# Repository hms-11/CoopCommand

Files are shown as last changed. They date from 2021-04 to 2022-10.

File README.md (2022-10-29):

# CoopCommand

# Development on this project has stopped. See [CoopCommand ESP32](https://github.com/hms-11/CoopCommandESP32) for the next generation controller and code.

Chickens are simple animals with lots of benefits. The downside? Humans are not the only creatures that find chickens tasty and chickens themselves require some basic maintenance and care to keep happy and healthy. 

CoopCommand aims to reduce the daily labour of looking after chickens, improve their well-being as well as allow hobby-farmers the ability to go out for the night without worrying if their chickens are in danger from wandering predators. 

Contributors always welcome, I could use people smarter than myself to keep improving this project. 

You can also support this project through "Buy me a Coffee": 

<a href="https://www.buymeacoffee.com/AutoHobbyFarm" target="_blank">Buy Me A Coffee</a>

In action: Here is a video of CoopCommand installed in my coop. https://www.youtube.com/watch?v=HNLnl-pNmuM

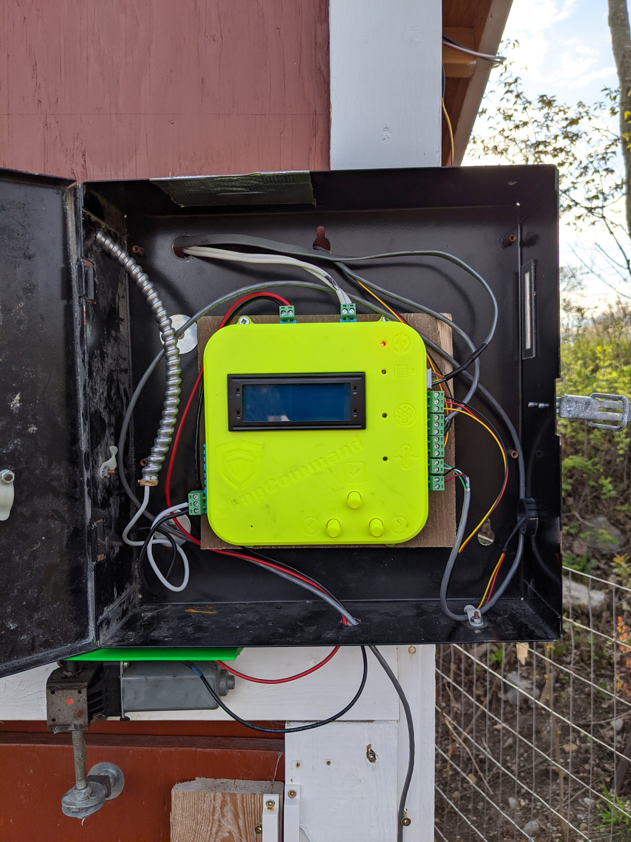
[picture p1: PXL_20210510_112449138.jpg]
CoopCommand Picture (https://github.com)


# GOALS:

- Ease of installation and configuration for non-technical individuals. 

- Multiple Power Options (wall wart mains power or 12-36V off-grid solar/wind/battery systems).

- Configuration settings saved in case of power-outage.

- Wi-Fi connectivity for remote monitoring and overriding of coop door.

- Camera for viewing inside of coop.

# FEATURES:

## COOP COMMAND MAIN BOARD:

- Pluggable Terminal Block connectors for all user-installed inputs/outputs.

- JST XH 5-pin for connection to CoopCam Wi-FI Camera Ad-On.

- DHT22 for interior coop temperature.

- DS18B20 for water temperature.

- GL5539 Photoresistor w/10K resistor voltage divider for daylight sensor.

- MAX3373 level shifting IC for Atmega-ESP32 serial communication.

- 7805 "footprint" - Actually uses either one of the drop in footprint compatible buck convertors or my own "MEGA7805" buck converter that can output up to 3A cont. 

- TI DRV8871 Motor Driver IC w/3.6A current cabilitity & voltages up to maximimum working voltage of CoopCommand.

- 20x4 LCD.

- I2C backpack integrated.

- 3 user input buttons.

- EEPROM for saving user settings.

- LayLight Relay for supplementing daylight hours to keep chickens laying even with less than 14 hours of Daylight.

- Ventilation Fan Relay for cooling the coop in the summer.

- Water Heat Relay for heating the water in the winter. 

- ATMEGA328P in DIP configuration, easily programmed through Arduino IDE.

## ESP32 COOPCAM:

- ESP32-CAM AI-THINKER based.

- Custom PCB for ESP-32-CAM to socket into, breaks out remaining GPIO's, breaks out serial header for programming and boot button as well as on-board bulk capacity (200UF).

- JST XH 5-pin Connector, identical pinout to mainboard side to allow cable to be plugged in either way.

- Wi-Fi connection through Blynk.

- Serial connection to main board.

## BLYNK:

- Override door open or closed.

- Take a picture with the CoopCam and display it in the app

- Monitor door status (Open, Closed, Opening/Closing).

# Getting Started:

All files are included in this git-repository to get CoopCommand up and running. To get started, use the Gerber files and BOM to get the PCB's coming. The pic n place files can be used if your board house supports assembly. These boards were designed to use JLCPCB's assembly service with as many "basic" components as possible. 

Once you have the boards in hand and assembled, see the programming notes file for instructions on how to load the code. ATTENTION: This guide assumes the ATMEGA328P has a bootloader already installed, if working with new, "bare" chips you will need to burn a bootloader before installing the sketch. 

For the ESP32-CAM "CoopCam" aspect, this guide from Random Nerd Tutorials outlines the steps for setting up a gmail account with the proper settings. https://randomnerdtutorials.com/esp32-cam-send-photos-email/ 
These settings, along with your wifi info and BLYNK authentication token will need to be put into the sketch for the camera. 

# CURRENT KNOWN ISSUES:

- Some Camera ribbon cables seem to be different lengths, some tweaking of CamLid file may be needed to ensure lens fits through housing.  

- The CoopCam and associated Blynk app should not be used at this point. Reboot can cause CoopCommand to go into manual door mode, leaving the door open at night. Main board functions fine running solo. 

# PLANNED UPGRADES:

- Figure out what is up with the multi-button press sometimes required. 

- Improved EEPROM setting saves with more user settings being saved to EEPROM (currently door close light level, water heat on and ventilation fan on temps are saved).

- "self configuration" of system on startup. I would like the door to run an initial cycle on first power-on so it can self test motor connections and adjust if connected "backwards" 

- Easy deployment of CoopCam. Would like users to log into a self-hosted website on the ESP32-Cam, input their Wifi info and Blynk Authorization certificate. then have the system reboot on their network, attached to their Blynk app.

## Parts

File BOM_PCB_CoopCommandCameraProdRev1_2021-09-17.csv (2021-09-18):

ID | Name | Designator | Footprint | Quantity | Manufacturer Part | Manufacturer | Supplier | Supplier Part
1 | 100uF | C1,C7 | CAP-SMD_L3.5-W2.8 | 2 | TAJB107K006RNJ | AVX | LCSC | C16133
2 | 100 | R1,R2 | R1206 | 2 | 1206W4F1000T5E | UniOhm | LCSC | C17901
3 | ESP32-CAM | CAM1 | ESP32CAM-SOCKET | 1 | https://github.com/raphaelbs/esp32-cam-ai-thinker | AI Thinker |  | https://github.com/raphaelbs/esp32-cam-ai-thinker
4 | MMBT5551_C2145 | Q1 | SOT-23-3_L2.9-W1.3-P1.90-LS2.4-BR | 1 | MMBT5551 | CJ | LCSC | C2145
5 | 100nF | C3,C4 | C0805 | 2 | CC0805KRX7R9BB104 | YAGEO | LCSC | C49678
6 | Button-Prog | SW1 | SW-TH_4PIN-L6.00-W6.00 | 1 | Switch,6*6*6Plastic head,260G, 0.25mm,Straight line | BBJ | LCSC | C71836
7 | MAX3373EEKA+T | U1 | SOT-23-8_L3.0-W1.7-P0.65-LS2.8-TL | 1 | MAX3373EEKA+T | Maxim Integrated | LCSC | C116658
8 | CONN_01X07 | J1 | HDR-M-2.54_1X7 | 1
9 | Programming Header 1x4 | H1 | HDR-TH_4P-P2.54-V | 1 | 210S-1*4P L=11.6MMGold-plated black | Ckmtw | LCSC | C124378
10 | USB-302S | USB1 | USB-A-SMD_USB-302S | 1 | USB-302S | SOFNG | LCSC | C112455
11 | 510 | R7 | R0805 | 1 | 0805W8F5100T5E | UniOhm | LCSC | C17734
12 | 10K | R8 | R0805 | 1 | 0805W8F1002T5E | UniOhm | LCSC | C17414
13 | HL-AF-5060H343W-3-S1-THL-HR3(3800-4250K) | LED1,LED2 | LED-ARRAY-SMD_6P-L5.4-W5.0-TL-FD | 2 | HL-AF-5060H343W-3-S1-THL-HR3(3800-4250K) | Hongli Zhihui (HONGLITRONIC) | LCSC | C219405
14 | 1uF | C2 | C0805 | 1 | CL21B105KBFNNNE | SAMSUNG | LCSC | C28323

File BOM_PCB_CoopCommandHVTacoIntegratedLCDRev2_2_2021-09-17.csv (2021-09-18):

ID | Name | Designator | Footprint | Quantity | Manufacturer Part | Manufacturer | Supplier | Supplier Part
1 | B3B-XH-A(LF)(SN) | CN14,CN13 | CONN-TH_3P-P2.50_B3B-XH-A-LF-SN | 2 | B3B-XH-A(LF)(SN) | JST Sales America | LCSC | C144394
2 | TS-1102S-B-H-B | SW1,SW2,SW3,SW4 | SW-SMD_4P-L6.0-W6.0-P4.50-LS11.0 | 4 | TS-1102S-B-H-B | XKB Enterprise | LCSC | C480275
3 | 1K | R12,R22,R21,R20,R19,R18 | R0402 | 6 | 0402WGF1001TCE | UniOhm | LCSC | C11702
4 | 10K | R3,R2,R17,R16,R15,R14,R13,R11,R10,R9,R1,R5 | R0402 | 12 | 0402WGF1002TCE | UniOhm | LCSC | C25744
5 | 100nF | C27,C24,C21,C23,C22,C20,C19,C18,C17,C16,C15,C14,C26,C9,C8,C5,C2,C1 | C0603 | 18 | CC0603KRX7R9BB104 | YAGEO | LCSC | C14663
6 | FC-2012HRK-620D | LED2,LED1,LED3 | LED0805-RD | 3 | FC-2012HRK-620D | NATIONSTAR | LCSC | C84256
7 | XY2500R-A-5.00-3P | CN5,CN3,CN2,CN1,CN12,CN11,CN8 | CONN-TH_XY2500R-A-5.00-3P | 7 | XY2500R-A-5.00-3P | -- | LCSC | C505798
8 | COOPCAM CONNECTOR | USB1 | USB-A-SMD_USB-302S | 1 | USB-302S | SOFNG | LCSC | C112455
9 | 2x3 ICSP HEADER | H2 | HDR-TH_6P-P2.54-V-R2-C3-S2.54 | 1 | Female header/2.54mm2x3 Female header | ReliaPro | LCSC | C47552
10 | 1x4 SERIAL PROGRAMMING HEADER | H1 | HDR-TH_4P-P2.54-V | 1 | 210S-1*4P L=11.6MMGold-plated black | Ckmtw | LCSC | C124378
11 | ATMEGA328P-AU | U1 | TQFP-32_L7.0-W7.0-P0.80-LS9.0-BL | 1 | ATMEGA328P-AU | MICROCHIP | LCSC | C14877
12 | 22pF | C4,C3 | C0402 | 2 | 0402CG220J500NT | FH | LCSC | C1555
13 | SM4007PL | D3,D4,D5 | SOD-123F_L2.8-W1.8-LS3.7-RD | 3 | SM4007PL | MDD | LCSC | C64898
14 | 220uF | C11 | CAP-SMD_BD6.3-L6.6-W6.6-RD | 1 | VES221M1CTR-0607 | LELON | LCSC | C127327
15 | 10K | R39,R40,R41,R8 | R0805 | 4 | 0805W8F1002T5E | UniOhm | LCSC | C17414
16 | 510 | R37,R38,R42,R7 | R0805 | 4 | 0805W8F5100T5E | UniOhm | LCSC | C17734
17 | 100uF | C7,C6 | CAP-SMD_L3.5-W2.8 | 2 | TAJB107K006RNJ | AVX | LCSC | C16133
18 | 16MHz | X1 | OSC-SMD_4P-L3.2-W2.5-BL | 1 | X322516MLB4SI | YXC | LCSC | C13738
19 | 10uH | L1 | L0603 | 1 | SDFL1608S100KTF | Sunlord | LCSC | C1035
20 | 3.24K | R4 | R0402 | 1 | 0402WGF3241TCE | UniOhm | LCSC | C11457
21 | 330 | R43,R44,R45 | R0805 | 3 | 0805W8F3300T5E | UniOhm | LCSC | C17630
22 | B4B-XH-A(LF)(SN) | CN4 | CONN-TH_B4B-XH-A (LF)(SN) | 1 | B4B-XH-A(LF)(SN) | JST Sales America | LCSC | C144395
23 | PCF8574T/3,518 | U3 | SOIC-16_L10.3-W7.5-P1.27-LS10.3-BL | 1 | PCF8574T/3,518 | NXP | LCSC | C7605
24 | 5K | R6 | RES-ADJ-TH_RM063-103 | 1 | RM063-103 10K | JML | LCSC | C38793
25 | 15uH | L2 | IND-SMD_L7.1-W6.6 | 1 | MWSA0603-150MT | Sunlord | LCSC | C132136
26 | 10uF | C12 | C0805 | 1 | CL21A106KAYNNNE | SAMSUNG | LCSC | C15850
27 | 20x4 LCD | LCD1 | DISP_LCD_4X20 | 1
28 | 10nF | C10 | C0402 | 1 | CL05B103KB5NNNC | SAMSUNG | LCSC | C15195
29 | TPS5430DDAR | U2 | SOIC-8_L5.0-W4.0-P1.27-LS6.0-BL-EP | 1 | TPS5430DDAR | TI | LCSC | C9864
30 | 100nF | C25 | C0805 | 1 | CC0805KRX7R9BB104 | YAGEO | LCSC | C49678
31 | XY2500R-B-5.00-2P | CN10,CN9 | CONN-TH_2P-P5.00_XY2500R-B-5.00-2P | 2 | XY2500R-B-5.00-2P | -- | LCSC | C505815
32 | SRD-05VDC-SL-C | RLY1,RLY2,RLY3 | RELAY-TH_SRD-XXVDC-XL-C | 3 | SRD-05VDC-SL-C | SONGLE | LCSC | C35449
33 | MMBT5551_C2145 | Q2,Q3,Q4,Q1 | SOT-23-3_L2.9-W1.3-P1.90-LS2.4-BR | 4 | MMBT5551 | CJ | LCSC | C2145
34 | SS34_C8678 | D2,D1 | DO-214AC_L4.3-W2.7-LS5.3-RD | 2 | SS34 | MDD | LCSC | C8678
35 | 330uF | C13 | CAP-TH_BD10.0-P5.00-D1.0-FD | 1 | 330uF 25V 10*13 | ValuePro | LCSC | C44600
36 | rz7899 | U4 | SOP-8_L4.9-W3.9-P1.27-LS6.0-BL | 1 | rz7899 | RZ | LCSC | C92373
37 | 4.7K | R23 | R0402 | 1 | 0402WGF4701TCE | UniOhm | LCSC | C25900

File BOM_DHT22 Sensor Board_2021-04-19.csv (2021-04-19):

ID | Name | Designator | Footprint | Quantity | Manufacturer Part | Manufacturer | Supplier | Supplier Part | Price | Voltage | Mounted | Description
1 | S3B-XH-A (LF)(SN) | CN1 | CONN-TH_S3B-XH-A-LF-SN | 1 | - | JST Sales America | LCSC | C157928 | 0.1003
2 | DHT22 | U1 | DHT22_AM2303_VERT | 1 |  | Aosong (Guangzhou) Electronics Co., Ltd. | AdaFruit | PRODUCT ID: 385 |  | 3.3V - 5.5V | Yes | Digital-output relative humidity & temperature sensor/module

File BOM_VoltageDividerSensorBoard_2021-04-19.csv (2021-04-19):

ID | Name | Designator | Footprint | Quantity | Manufacturer Part | Manufacturer | Supplier | Supplier Part | Price | LCSC Assembly | Assembly Type | Paste Type
1 | S3B-XH-A (LF)(SN) | CN1 | CONN-TH_S3B-XH-A-LF-SN | 1 | - | JST Sales America | LCSC | C157928 | 0.1003
2 | GL5539(40-50) | R1 | RES-TH_L5.1-W4.3-P3.40_GL55 | 1 | GL5539(40-50) | ReliaPro | LCSC | C10079 | 0.0482
3 | 10K | R2 | RES-TH_BD2.4-L6.3-P10.30-D0.6 | 1 | RN 1/4W 10K F T/B A1 | TyoHM | LCSC | C410695 | 0.007012 | Yes | manualWeld | expand

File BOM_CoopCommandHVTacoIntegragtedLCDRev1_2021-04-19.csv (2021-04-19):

ID | Name | Designator | Footprint | Quantity | Manufacturer Part | Manufacturer | Supplier | Supplier Part
1 | 22pF | C10,C17 | C0805 | 2 | CL21C220JBANNNC | SAMSUNG | LCSC | C1804
2 | 330uF | C13 | CAP-TH_BD10.0-P5.00-D1.0-FD | 1 | 330uF 25V 10*13 | ValuePro | LCSC | C44600
3 | 1uF | C2,C19 | C0805 | 2 | CL21B105KBFNNNE | SAMSUNG | LCSC | C28323
4 | 100nF | C1,C3,C4,C6,C8,C9,C11,C16,C20,C21,C22,C25,C26,C27,C28,C29,C30,C31,C32 | C0805 | 19 | CC0805KRX7R9BB104 | YAGEO | LCSC | C49678
5 | 100uF | C23,C24 | CAP-TH_BD6.3-P2.50-D1.0-FD | 2 | SPT1VM101E12OR | Yunxing | LCSC | C698171
6 | S5B-XH-A-1 (LF)(SN) | CN1 | CONN-TH_S5B-XH-A-1-LF-SN | 1 | - | JST Sales America | LCSC | C163038
7 | B4B-XH-A(LF)(SN) | CN6 | CONN-TH_B4B-XH-A (LF)(SN) | 1 | B4B-XH-A(LF)(SN) | JST Sales America | LCSC | C144395
8 | XY2500R-B-5.00-2P | CN2,CN3,CN9,CN10 | CONN-TH_2P-P5.00_XY2500R-B-5.00-2P | 4 | XY2500R-B-5.00-2P | -- | LCSC | C505815
9 | XY2500R-A-5.00-3P | CN8,CN11,CN12,CN13,CN14,CN15 | CONN-TH_XY2500R-A-5.00-3P | 6 | XY2500R-A-5.00-3P | -- | LCSC | C505798
10 | SS34_C8678 | D1 | DO-214AC_L4.3-W2.7-LS5.3-RD | 1 | SS34 | MDD | LCSC | C8678
11 | SM4007PL | D5,D6,D7 | SOD-123F_L2.8-W1.8-LS3.7-RD | 3 | SM4007PL | MDD | LCSC | C64898
12 | Programming Header 1x4 | H1 | HDR-TH_4P-P2.54-V | 1 | 210S-1*4P L=11.6MMGold-plated black | Ckmtw | LCSC | C124378
13 | JQ1P-5V-F | K4,K5,K6 | RELAY-TH_JQ1P-5V-F | 3 | JQ1P-5V-F | PANASONIC | LCSC | C58271
14 | MGGB2012M181HT-LF | L2 | L0805 | 1 | MGGB2012M181HT-LF | microgate | LCSC | C486339
15 | DISP_LCD | LCD1 | DISP_LCD_4X20 | 1
16 | FC-2012HRK-620D | LED3,LED4,LED5,LED6 | LED0805-RD | 4 | FC-2012HRK-620D | NATIONSTAR | LCSC | C84256
18 | MMBT5551_C2145 | Q4,Q5,Q6 | SOT-23-3_L2.9-W1.3-P1.90-LS2.4-BR | 3 | MMBT5551 | CJ | LCSC | C2145
19 | 1K | R6,R27,R28,R31,R33,R35 | R0805 | 6 | 0805W8F1001T5E | UniOhm | LCSC | C17513
20 | 30K | R7 | R0805 | 1 | 0805W8F3002T5E | UniOhm | LCSC | C17621
21 | 330 | R8 | R0805 | 1 | SYLE0805JN330RP | SANYEAR | LCSC | C385915
22 | 10K | R16,R25,R26,R29,R30,R32,R34,R36,R39,R40,R41 | R0805 | 11 | 0805W8F1002T5E | UniOhm | LCSC | C17414
23 | 510 | R37,R38,R42 | R0805 | 3 | 0805W8F5100T5E | UniOhm | LCSC | C17734
24 | 330 | R43,R44,R45 | R0805 | 3 | 0805W8F3300T5E | UniOhm | LCSC | C17630
25 | Button-Reset | SW1 | SW-TH_4PIN-L6.00-W6.00 | 1 | Switch,6*6*6Plastic head,260G, 0.25mm,Straight line | BBJ | LCSC | C71836
26 | Button-6x6x6mm | SW5,SW6,SW7 | SW-TH_4PIN-L6.00-W6.00 | 3 | Switch,6*6*6Plastic head,260G, 0.25mm,Straight line | BBJ | LCSC | C71836
27 | ATMEGA328P-PU | U1 | DIP-28_L34.6-W7.3-P2.54-LS10.2-BL | 1 | ATMEGA328P-PU | MICROCHIP | LCSC | C33901
28 | MAX3373EEKA+T | U4 | SOT-23-8_L3.0-W1.7-P0.65-LS2.8-TL | 1 | MAX3373EEKA+T | Maxim Integrated | LCSC | C116658
29 | L7805CV | U5 | TO-220-3_L10.0-W4.5-P2.54-L | 1 | L7805CV | STMicroelectronics | LCSC | C111887
30 | DRV8871DDAR | U6 | SO-8_L4.9-W3.9-P1.27-LS6.0-BL-EP | 1 | DRV8871DDAR | TI | LCSC | C75864
31 | 16MHZ | X1 | HC-49S_L11.0-W4.4-P4.88 | 1 | 5S0-1600A1620-00 | XTY | LCSC | C389708
33 | I2C "BackPack" | P1 | HDR-TH_16P-P2.54-V | 1 | N/A | N/A | NA | N/A

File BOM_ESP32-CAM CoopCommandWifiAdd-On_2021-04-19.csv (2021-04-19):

ID | Name | Designator | Footprint | Quantity | Manufacturer Part | Manufacturer | Supplier | Supplier Part | Price | LCSC Assembly | Assembly Type | Paste Type
1 | 100uF | C1,C2 | CAP-TH_BD6.3-P2.50-D1.0-FD | 2 | SPT1VM101E12OR | Yunxing | LCSC | C698171 | 0.116038
2 | S5B-XH-A-1 (LF)(SN) | CN1 | CONN-TH_S5B-XH-A-1-LF-SN | 1 | - | JST Sales America | LCSC | C163038 | 0.1102 | Yes | manualWeld | expand
3 | Programming Header 1x4 | H1 | HDR-TH_4P-P2.54-V | 1 | 210S-1*4P L=11.6MMGold-plated black | Ckmtw | LCSC | C124378 | 0.0261
4 | Breakout Header 1x9 | H2 | HDR-TH_9P-P2.54-V | 1 | 2.54mm 1*9 Straight Female header | BOOMELE | LCSC | C39576 | 0.0569 | Yes | manualWeld | expand
5 | Button-Prog | SW1 | SW-TH_4PIN-L6.00-W6.00 | 1 | Switch,6*6*6Plastic head,260G, 0.25mm,Straight line | BBJ | LCSC | C71836 | 0.0181
6 | ESP32-CAM | U1 | ESP32-CAM | 1

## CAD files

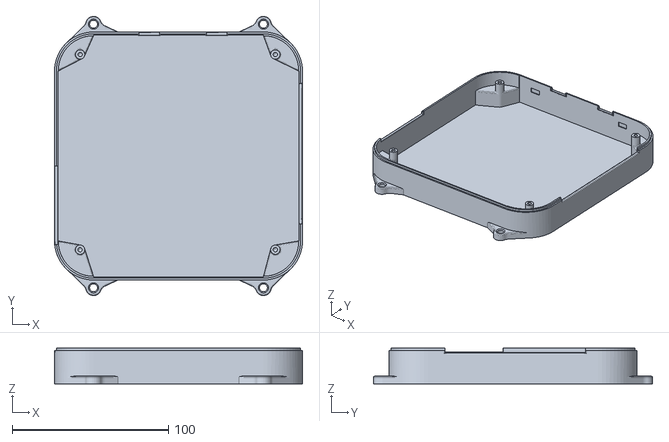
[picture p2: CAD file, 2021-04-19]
MainBody.stl
158.8 x 178.8 x 23.0

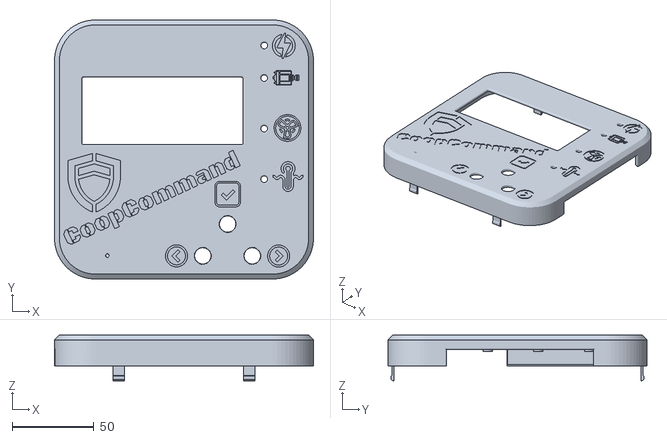
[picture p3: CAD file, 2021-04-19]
MainLid.stl
158.8 x 158.8 x 28.2

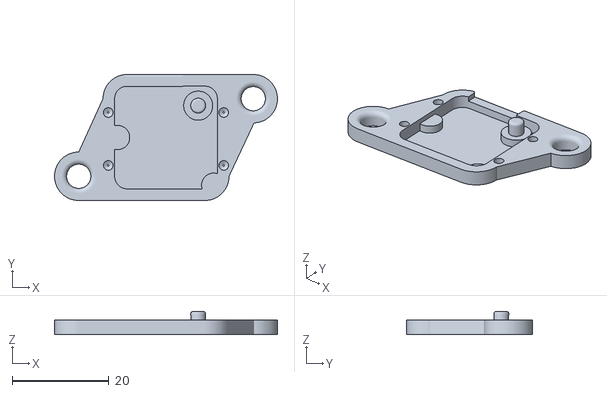
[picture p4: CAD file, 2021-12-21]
TempBottom.stl
46.0 x 26.0 x 4.80

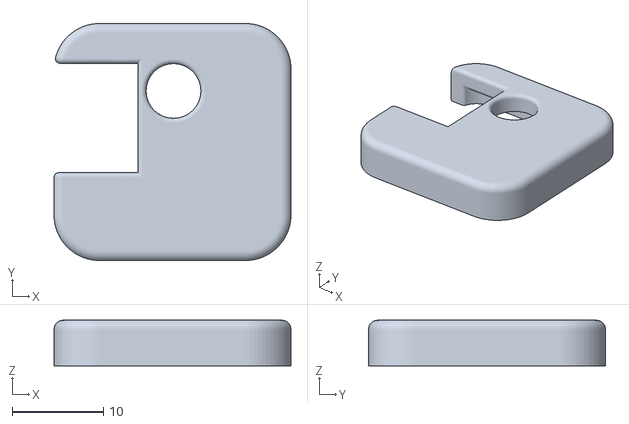
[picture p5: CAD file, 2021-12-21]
PhotoCellTop.stl
26.0 x 26.0 x 5.00

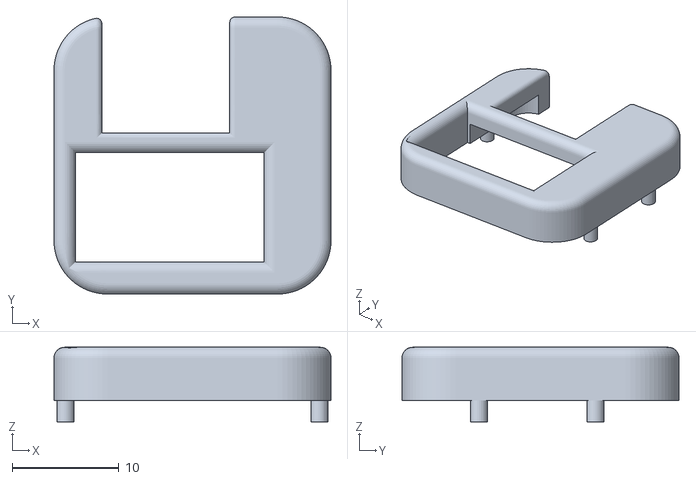
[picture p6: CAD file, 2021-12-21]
TempTop.stl
26.0 x 26.0 x 7.00

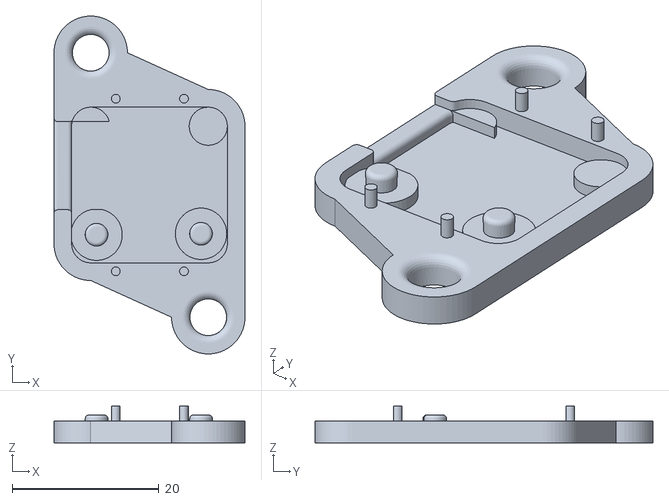
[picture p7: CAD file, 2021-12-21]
PhotoCellBottom.stl
26.0 x 46.0 x 5.00

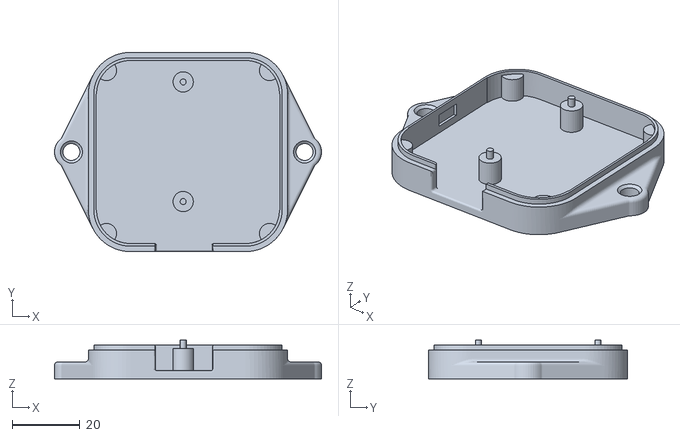
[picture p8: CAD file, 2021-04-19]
CamBody.stl
78.8 x 58.8 x 11.4

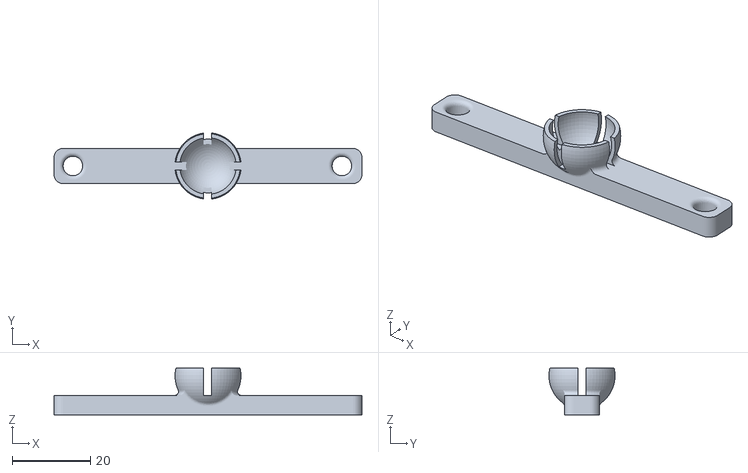
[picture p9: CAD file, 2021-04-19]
CamMountSocket.stl
78.8 x 16.9 x 12.0

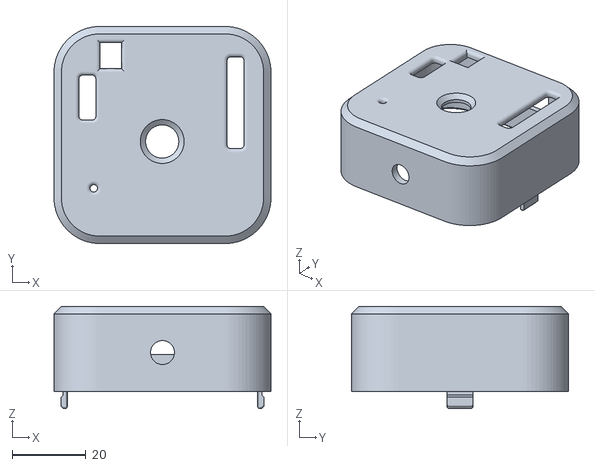
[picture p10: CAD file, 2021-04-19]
CamLid.stl
58.8 x 58.8 x 27.7

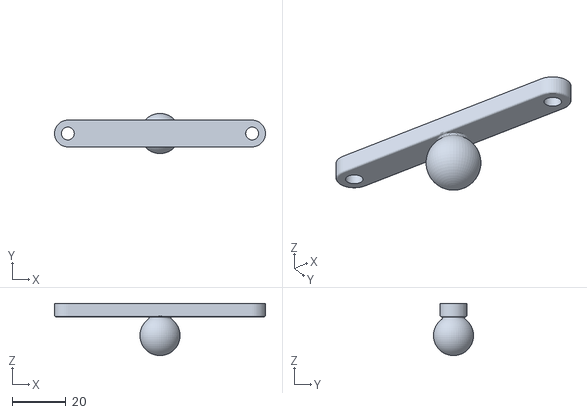
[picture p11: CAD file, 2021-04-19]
CamMountBall.stl
78.8 x 15.0 x 19.5

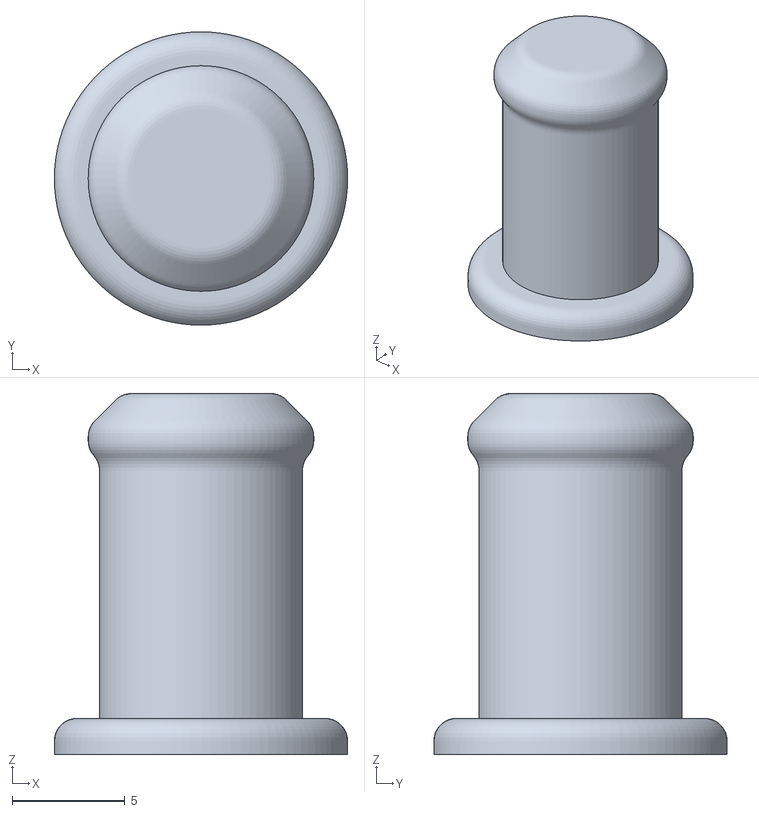
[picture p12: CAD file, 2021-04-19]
Button.stl
13.0 x 13.0 x 16.0

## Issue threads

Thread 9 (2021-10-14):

Assembly of your board

RolandWijnen, 2021-10-14:
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
Hi hms-11,

I like your CoopCommand project and decided to build it too. I've ordered almost all of the stuff from the BOM, got the enclosure 3D printed, and ordered the board as well. I'm now about to assemble the board. I'll be soldering all the components myself. Could you share a couple of 'assembly instructions' as well? Most of the stuff is pretty straightforward, but I have a couple of questions:

1. I don't see how exactly you assembled the LCD. I've one with the Backpack attached to it. Have you connected the backpack with jumper wires to CN6. I cannot really figure that out [from this photo](https://www.hackster.io/news/coopcommand-is-a-diy-device-that-controls-chicken-coops-76a8319db548).
2. The switches on the BOM are 6mm high. The ones you've assembled on the board seem to be a bit higher. Will the 6mm high switches work or should I get 'taller' ones?
3. What bolts are you using to fix the LCD and the board to its enclosure. Just want to make sure that I'm using the right bolts so that the LCD nicely sits in the enclosure.
Would be great if you could help me out to assemble all of this. The physical door is already finished. It just badly needs some CoopCommand :-) Thanks for your help.

hms-11, 2021-10-16:
Hello! Sorry for the late reply. I'm away from the house for a couple days
but will be back on Monday. I'll send you some pictures and details as soon
as I get back.

Thanks for the interest in my project!

Oct. 14, 2021, 2:01 p.m. RolandWijnen, ***@***.***> wrote:

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

RolandWijnen, 2021-10-31:
Hi, thanks for your reply and specific answers. I've ordered an LCD with a separate backpack and a set of bolts. So, for now I'm ok. Once I have the components in, I can start working on soldering everything on the board. If you would be able snap some pictures later that would be great. Otherwise, I'll just reconnect here if I run into something. Enjoy your Sunday!

hms-11, 2021-11-10:
Hello @RolandWijnen!

I snapped a couple photos that show the mounting of the LCD. As you can see I used a male header on the board so that the LCD was replaceable without soldering should it have an issue due to weather, chickens, etc.
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

The board is still mounted but I'm hoping to swap it out for a slightly newer version I'm prototyping this weekend. When it comes out, I'll snap some photos of the back of the board as well so you can see the I2C "backpack" adapter location and wiring.
Let me know if you run into any other issues and I'll try to help to the best of my ability!

Closed 2021-12-19.

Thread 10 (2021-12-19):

Which LiquidCrystal I2C Library is required?

RolandWijnen, 2021-12-19:
Hi,

I've assembled the entire board and I'm now ready to compile the code. Which LiquidCrystal_I2C is required. I've included the one from Frank de Brabander. This gives the compilation error below. Any suggestions? Thanks!

`Arduino: 1.8.12 (Mac OS X), Board: "Arduino Nano, ATmega328P"

Warning: Board breadboard:avr:atmega328bb doesn't define a 'build.board' preference. Auto-set to: AVR_ATMEGA328BB
/Users/roland/Dropbox (Personal)/Smart Living/CoopCommand/CoopCommandWifiRev1/CoopCommandWifiRev1.ino: In function 'void setup()':
CoopCommandWifiRev1:147:13: error: no matching function for call to 'LiquidCrystal_I2C::begin()'
   lcd.begin();
             ^
In file included from /Users/roland/Dropbox (Personal)/Smart Living/CoopCommand/CoopCommandWifiRev1/CoopCommandWifiRev1.ino:22:0:
/Users/roland/Documents/Arduino/libraries/LiquidCrystal_I2C/LiquidCrystal_I2C.h:58:8: note: candidate: void LiquidCrystal_I2C::begin(uint8_t, uint8_t, uint8_t)
   void begin(uint8_t cols, uint8_t rows, uint8_t charsize = LCD_5x8DOTS );

        ^~~~~
/Users/roland/Documents/Arduino/libraries/LiquidCrystal_I2C/LiquidCrystal_I2C.h:58:8: note:   candidate expects 3 arguments, 0 provided
exit status 1
no matching function for call to 'LiquidCrystal_I2C::begin()`

hms-11, 2021-12-21:
Hello,
Sorry for the delay in answering, I was away from my computer for the weekend.
The Library I am using is this one, which seems to be from Fran de Brabander as well so it is likely the same.
https://github.com/fdebrabander/Arduino-LiquidCrystal-I2C-library

I am working on a windows machine but no idea why that would cause an issue...

Do the example sketches for the library compile without error?

RolandWijnen, 2021-12-21:
Hi hms-11,
No worries. Good to know I'm using the correct library. I'll dig into the compile error a little bit deeper. I'll let you know what I find. Thanks for now!

RolandWijnen, 2022-04-17:
Hi there again,

I've been working on some other projects in my garden in the meantime. Right now working on CoopCommand again. I was able to compile the code now, also for CoopCam. Both were successfully uploaded to the boards.

Closed 2022-04-17.

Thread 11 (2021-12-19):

Housing for sensors, switches (top and bottom), and the ESPCAM board

RolandWijnen, 2021-12-19:
Hi,

I've made good progress with the assembly of the main board as mentioned in my other post. I have a couple of questions related to bringing everything together;

1.  How are your sensor boards (SkyEye, DHT22) setup? Did you put them in a standard enclosure?

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

2. What switches did you use for detecting whether the door is at top and bottom? I did not see these components in your BOMs. Can you send me a picture of how these are mounted on your chicken coop?

3. How should the ESPCAM board be assembled? On this photo (https://hackster.imgix.net/uploads/attachments/1290503/czvqlbh_giJi0WB0Rl.jpeg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) I see that you've mounted the components on the backside of the PCB. Is that the right way? Or should the components be mounted to the side printed with text and symbols. See the photo below.

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

Thanks in advance for your support!

RolandWijnen, 2021-12-19:
I think I've solved Question 3 already. The ESP board needs to be on the other side so that the pins correspond with the board layout. I guess the other components, except the connector, also need to be on the other side so that everything fits in the housing. Is that correct?

hms-11, 2021-12-21:
Yeah, that version of the ESP board needs to be mounted as described. An unfortunate footprint error in my pcb design software means everything but the connector needs to be mounted on the back side of the board.

I made some small 3D printed enclosures for the sensor boards. The photocell one I also coated with a waterproof coating (nail polish works fine) before putting it in the enclosure. I just uploaded the 3D files for those pieces to the repository.

I used Normally Closed (NC) magnetic reed switches for the door. The best way I found to buy them was as "magnetic security door sensors" as they are called here. Then you get a rugged housing and easy mounting as well. I went with these switches because they can't gum up or otherwise blocked/plugged.
Here is an example of what I used:
https://www.amazon.ca/Uxcell-a14060400ux0169-Magnetic-Door-Switch/dp/B00PZMG980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

RolandWijnen, 2021-12-21:
Thanks for the quick reply and info! I'll probably put the sensors in a standard enclosure. I've also ordered the reed switches.

I've already been playing around with Blynk and created the interface based on your notes. I also setup my own local Blynk server so that I don't depend on the cloud :-)

Looking at the code to better understand how CoopCommand interfaces with the ESPCam, I thought about the following. The ESPCam board can also be flashed with ESPHome. ESPHome is fairly simple to program so that it interfaces with CoopCommand over the UART bus (as it is working now). This would integrate seamlessly with my Home Assistant.

This made me think about making CoopCommand more dynamic by sending the sensor readings: temp, humidity, watertemp, illuminance) every 30 minutes or so. I could then show the cam feed and sensor information on a nice card in the Home Assistant interface.

Have you considered using ESPHome => https://esphome.io/? It might make it easier to deploy ESPCam that using Blynk. Curious to hear your thoughts on this.

Closed 2022-04-18.

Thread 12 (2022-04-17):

Hardware and software checks?

RolandWijnen, 2022-04-17:
Hi,

I've been able to compile and upload the code to CoopCommand and CoopCam. When I plug in power (12V) the LCD lits up for 2 seconds and then goes black. Is there a way to test the CoopCommand and CoopCam board separately. I've hooked up TX and RX to look at the SerialMonitor but nothing to see there.

Are there some hardware checks that I can do? Software checks after that? Would appreciate your help, once again. Thanks!!

RolandWijnen, 2022-07-17:
Hi hms-11,

Any suggestions for checks? Thanks a lot!

Best regards, Roland.

hms-11, 2022-07-19:
Hey Roland!

I am so sorry for the delay, somehow I completely missed your initial
request!

Is there a chance you can upload some high-resolution images so I can take
a peak?

What are you using as a 12v supply? I would check to make sure that you
have 5v at the 5v pin for the LCD to make sure it is getting the proper
voltage. The fact that it lights up and then blanks out seems odd and
almost like the power supply is tripping due to overcurrent for some reason.

Sorry again for not responding sooner!

Corey

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

RolandWijnen, 2022-07-22:
Hi Corey!

No worries. I'll upload some photos tomorrow. I've connected a (led) power supply of 12V 80W. The display only flashes and then the motor starts turning, switching direction every couple of seconds. It seems that the code is stuck in some loop.

I also noticed earlier that the ESPCam came online on my Wifi, but now it does not appear anymore.

To be continued...

RolandWijnen, 2022-07-23:
Hi Corey,

Here are some photos from the board.

Let me know what you think...

Thanks, Roland.

[attachments (6).zip](https://github.com/hms-11/CoopCommand/files/9174610/attachments.6.zip)

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

RolandWijnen, 2022-07-29:
Hi Corey,

I've uploaded some hi-res picture as you can see. What do you think?

Cheers, Roland.

hms-11, 2022-08-09:
Hey @RolandWijnen, I had a chance to look through your images.
There are a couple questionable solder joints and places where I feel a short could have been introduced.

Do you have access to a multimeter? It would be nice to check if you have 5v on all the pins that expect them and GND continuity at all the GNDs

The odd behavior makes me think the system is constantly rebooting, or is getting pins pulled high or low by a solder short somewhere.

RolandWijnen, 2022-08-09:
Hey Corey,

Thanks, I'll check this later next week. I'll let you know what I find. Thanks again!

hms-11, 2022-08-10:
Hey @RolandWijnen, one other thought.

Have you seen what it is outputting in the serial monitor during this? If you fire up the Arduino IDE and have your programmer connected while the strange behavior is happening (only hook up RX, TX and GND if you are feeding it 12v power at the same time). That might also give us some hints as to what is going on.

Let me know what you discover!

Corey

RolandWijnen, 2022-08-19:
I don't see anything on the serial monitor of the mainboard. I've also checked the serial monitor of the ESPcam. This is the output. It indeed is rebooting all the time. There is also something wrong with camera config. I'll further investigate.

`10:24:22.398 -> Rebooting...
10:24:22.398 -> ets Jun  8 2016 00:⸮&⸮⸮S⸮
10:24:22.398 -> rst:0xc (⸮W_CPU_RESET⸮I⸮⸮⸮:0x13 (SPI_FAST_FLASH_BOOT)
10:24:22.398 -> configsip: 0, SPIWP:0xee
10:24:22.398 -> clk_drv:0^⸮b⸮}⸮⸮⸮鰼⸮b"⸮drv:0^⸮b ⸮⸮_drv:⸮⸮0⸮⸮}⸮⸮}⸮⸮⸮0⸮ }⸮⸮⸮⸮0x00
10:24:22.398 -> mode:DIO, clock div:1
10:24:22.398 -> load:0x3fff0030,len:1s24
10:24:22.398 -> ho 0 t⸮Z
⸮⸮⸮roo⸮j
10:24:22.398 -> load:0x4007800⸮⸮⸮⸮u1;508⸮⸮⸮+⸮⸮0x40⸮⸮⸮⸮⸮bb⸮⸮⸮3604
10:24:22.473 -> entry 0x400805f0
10:24:22.787 -> E ⸮⸮⸮⸮	 ⸮⸮}⸮⸮⸮⸮ cam_dma_config(280): frame buffer malloc failed
10:24:22.787 -> e (133)⸮⸮⸮_hal> cam_c⸮⸮⸮g(36⸮J' ⸮}%⸮⸮ ⸮⸮⸮kg f⸮-⸮⸮⸮H⸮⸮(134) camera: Camera config failed with error 0⸮⸮⸮⸮˙⸮⸮

10:24:27.642 -> C⸮⸮͕⸮сfailed: tgpip_send_msg_wait߮V
J⸮Fi⸮{pon΋ͽlwip/lwi⸮i⸮c/api/tcpip.c:455 (I⸮valid mbox)
10:24:27.642 ->
10:24:27.642 ->
10:24:27.642 -> Backtrace:0x40&⸮⸮⸮⸮z0x3ffb25100x4008bf15:0x3ffr⸮53X⸮Lq⸮⸮ʷ⸮⸮⸮⸮fb6550a0x400e87d6:0x3ffb2680 0x400f8651:0x3ffb26b0 0x400f86⸮L'⸮⸮ffb26d0 0x400e7fc9:0x⸮⸮⸮⸮7Y2⸮⸮500Z⸮⸮⸮҂⸮⸮ffb2⸮
10:24:27.738 -> ⸮⸮⸮0⸮ S⸮⸮҂⸮⸮ffb2790 0x400d37ed:0x3ffb27c0 0x400d3f69:0x3⸮⸮⸮8& ⸮⸮⸮⸮0d6\⸮҂z3ffbN⸮⸮ n
10:24:27.738 ->
10:24:27.738 ->
10:24:27.738 ->
10:24:27.738 ->
⸮Qʁ⸮ile SHC25⸮'$⸮⸮⸮⸮⸮⸮⸮⸮⸮⸮⸮⸮⸮⸮⸮j
10:24:27.738 ->
10:24:27.738 -> Rebooting...
10:24:27.738 -> ets Jun  8 2016 00:2⸮⸮⸮SH⸮HH⸮⸮⸮0xc ⸮⸮⸮5⸮U⸮⸮⸮ Q⸮,⸮⸮⸮0x⸮&B⸮A⸮_F⸮⸮⸮e1 M!}⸮OOT)
10:24:27.738 -> configsip: 0, SPIWP:0xee
10:24:27.738 -> clk_drv:0x00,q_drv:0⸮⸮b"⸮drv:p⸮0,c_⸮⸮⸮⸮:0x0&	⸮}irv:0⸮⸮b⸮⸮}⸮⸮⸮⸮0x00
⸮[⸮⸮颩⸮	 ⸮⸮⸮⸮⸮div:1
10:24:27.738 -> load:0x3fff0030,len:1324
10:24:27.738 -> ho 0 tail 12 room 4
10:24:27.738 -> load⸮⸮⸮0⸮ ⸮⸮⸮⸮len:13508⸮!⸮+⸮}⸮⸮ ⸮⸮⸮⸮jb⸮⸮⸮sO⸮j
10:24:27.738 -> entry 0x400805f0
10:24:28.086 -> E (c33) c⸮[E⸮⸮⸮ cam_dma_⸮⸮˥⸮⸮280): frame buffer malloc failed
10:24:28.086 -> E (133) cam_hal: cam_confi⸮J& SI  ⸮⸮}⸮⸮⸮}⸮⸮⸮⸮⸮⸮⸮⸮⸮
⸮⸮

10:24:28.086 -> E ⸮⸮&SE⸮⸮⸮⸮Ʌ⸮ ⸮X[Y⸮⸮config failed with error 0xffffffff
10:24:32.938 ->
10:24:32.938 -> assert failed: tcpip_send_msg_wa⸮⸮5⸮⸮⸮%  ⸮co⸮⸮˫⸮⸮ͽlwip/lwip/src/api/tcpipnc⸮Sk⸮⸮Inv⸮+⸮⸮mbox)
10:24:32.938 ->
10:24:32.938 ->
10:24:32.938 -> Backtrace:0x40083649:0x3ffb25100x4008bf15:0x3ffb2530 0x40091O⸮҂⸮⸮ff⸮⸮SS ⸮⸮Ѹ⸮ ⸮⸮⸮⸮p⸮⸮⸮N'⸮⸮0 0⸮ ⸮2⸮651:0x3ffb26b0 0x400f86b1:0x3ffb26d0 0x400e7fc'' ⸮f⸮,⸮⸮⸮`0x400d57⸮''&⸮fgb⸮
10:24:33.030 -> ⸮⸮00d4177:0x3ffb2798⸮0x4⸮Lֺ*⸮⸮0x3ffb27c0 0x400d3f69:0x3ffb2800 0x400d6db1⸮⸮⸮ffb2820
10:24:33.030 ->
10:24:33.030 ->
10:24:33.030 ->
10:24:33.030 ->
10:24:33.030 -> ELF file SHA256: 00⸮ ⸮08⸮⸮⸮⸮00⸮C⸮⸮R⸮⸮⸮K⸮⸮⸮⸮..
10:24:33.030 -> ets Jun  8 2016 00:22:57
10:24:33.030 ->
10:24:33.030 -> rst:0xc (SW_c⸮U%UM Q⸮,boot⸮&ų i ⸮}  MS} 1 M⸮_BOOT)
10:24:33.030 -> c⸮˥⸮ͥ⸮; 0,"SPIWP:0xee
10:24:33.030 -> clk_drv:0x00,q_drv:0x00,d_drv:0x00,cs0_drv:0x00K⸮}⸮⸮⸮⸮⸮⸮0,w^E⸮⸮;0x0pC⸮닕⸮DIO, clock d⸮⸮⸮j⸮⸮+⸮⸮0x3fff0030,len:1324
10:24:33.030 -> ho 0 tail 12 room 4
10:24:33.030 -> load:0x40078000,len:13508
10:24:33.030 -> l+⸮⸮0x⸮⸮¢⸮⸮⸮bb⸮⸮⸮3604
10:24:33.030 -> ⸮⸮⸮夘x400805f⸮C⸮E⸮⸮L⸮⸮	 ⸮⸮⸮hal: c⸮[E⸮⸮}⸮⸮⸮⸮⸮⸮IJ⸮ 2Ʌ⸮⸮⸮b_⸮V⸮⸮malloc failed
10:24:33.381 -> E (133) cam_hal: cam_config(364): cam_dma_config faile⸮c⸮ ⸮134) camera: Cq[Y⸮⸮gonfi⸮2⸮⸮le⸮HW⸮⸮ errK⸮0xffffffff
10:24:38.255 ->
10:24:38.255 -> assert failed: tcp⸮}͕⸮⸮}⸮͝}݅⸮⸮}͕⸮⸮IDF/compone⸮׽lwip/lwip/src/api/tcpip.c:47⸮ (Kn⸮X+⸮⸮mbox)⸮⸮C⸮HH*k⸮⸮race:0x40083649:0x3ffb25100x4008bf15:0x3ffb2530 0~}⸮_⸮⸮⸮⸮⸮~&⸮⸮⸮g⸮ ⸮3⸮[⸮⸮['⸮⸮ffb2680 0x400f8671:0x3f⸮b26⸮ ⸮⸮⸮00f86b1:0x3ffb26d0 0x400e7fc9:0x3ffb2720 0x400d⸮778:0x3ffb2740 0x400d4177:0x3ffb2790 0x40⸮ֺ⸮⸮⸮0x3ffb27c⸮⸮⸮⸮00d3f69:0x3ffb2800 0x400d6db1:0x3ffb2820
10:24:38.255 ->
10:24:38.255 ->
10:24:38.255 ->
10:24:38.401 ->
10:24:38.401 -> ⸮{c⸮_9⸮⸮ɻ⸮⸮&2⸮&&⸮⸮q⸮⸮b⸮3⸮HHU⸮⸮⸮⸮ung...⸮⸮ets"⸮]
 ⸮ ⸮⸮⸮⸮ ⸮⸮Ғ⸮Ҫ⸮j
10:24:38.401 ->
10:24:38.401 -> rst:0xc (SW_CPU_RESET),boot:0x13 (SPI_FAST_FLASH_BOOT)
10:24:38.401 -> configsip:⸮b ⸮A%⸮P:⸮⸮VVHh⸮k⸮%⸮⸮⸮⸮⸮,q_drv:0x00,d_drv:0x00,cs0_drv:0x00,hd_drv:0x00,wp_drv⸮l⸮0 s닫uDIOl⸮,⸮k⸮⸮dyv:1
⸮⸮+⸮⸮0x3fnf0030,len:132k
10:24:38.401 -> ho⸮L⸮⸮⸮⸮⸮12 room 4
10:24:38.401 -> load:0x40078000,len:13508
10:24:38.401 -> load:0x40080400,len:3604
10:24:38.401 -> ⸮⸮⸮0x40⸮805f0
10:24:38.696 -> E (133⸮҅⸮}⸮⸮⸮⸮ cam_dma_config(28⸮J'2Ʌ⸮⸮⸮buffer mall c failed
10:24:38.696 -> E (133) cam_hal: cam_config(364): cam_dma_config failed
10:24:38.696 -> E (⸮&S	⸮⸮⸮⸮Ʌ⸮ Ca⸮Y⸮⸮config failed wi⸮\*⸮⸮.⸮xffff⸮⸮⸮V⸮
10:24:43.556 -> assert⸮V⸮⸮⸮⸮⸮ tcpip_send_msg_ ait_sem IDF/components/lwip/lwip/src/api/⸮,⸮⸮⸮c:455 (Invalid mbox)
10:24:43.556 ->
10:24:43.556 -> C!⸮⸮⸮⸮Ʌ⸮e:0x40083⸮S҂⸮⸮ffb25100x4008bf15:0x3ffb2530 0x400913b9:0x3ffb25
0⸮L⸮ ⸮⸮8⸮9⸮⸮⸮⸮⸮⸮⸮2v>0 0𚘚⸮⸮SS҂⸮⸮ffb26b0 0x400f86b1:0x3ff⸮&   ⸮⸮⸮00e7fc9:0x3ffb2720 0x400d4778:0x3ffb2740 0x400d4177:0⸮&⸮⸮⸮⸮ʂ ⸮⸮Ѱ0⸮S ⸮⸮⸮⸮ffb27⸮ ⸮⸮⸮0⸮֚⸮9:⸮⸮ffb2800 0x400d6db1:0x3ffb2820
10:24:43.556 ->
10:24:43.556 ->
10:24:43.655 ->
10:24:43.655 ->
10:24:43.655 -> ELF file SHA256: 000⸮&⸮⸮⸮1L&⸮⸮⸮5Jy⸮⸮ﯹ⸮⸮⸮]⸮⸮ets Jun  < 2016 00:22:57
10:24:43.655 ->
10:24:43.655 -> rst:0xc (SW_⸮U⸮%UM Q⸮,boot:0x13 (SPI_FAST_FLASH_BOOT)
10:24:43.655 -> configsip: 0, ⸮⸮⸮ ⸮⸮⸮5
10:24:43.655 -> clk_drv:0x00,q_⸮.⸮⸮x00,d⸮Y.⸮⸮⸮⸮0,cs0_drv:0x00,hd_drv:0x00,wp_drv:0x00
10:24:43.655 -> mode:DIO, clock d闊j)loa⸮⸮⸮ff⸮⸮⸮⸮bb⸮⸮y⸮&&⸮
10:24:43.655 -> ho ⸮⸮W⸮⸮⸮12 room 4
10:24:43.655 -> load:0x40078000,len:13508
10:24:43.655 -> load⸮⸮⸮0080400,len:3604
10:24:43.655 -> entry 0x400805f0
10:24:43.962 -> E (133) cam_hal: cam_dma_confiw(280)⸮ frame ⸮]⸮v⸮⸮manvk⸮⸮XZ⸮⸮
10:24:43.962 -> E (133) ⸮X[⸮⸮⸮⸮acam_config(364): cam_dma_⸮⸮˥⸮⸮failed
10:24:43.962 -> E (134) camera: Camera conf⸮
Ʌ⸮⸮⸮⸮⸮with error ⸮⸮⸮⸮⸮⸮⸮⸮⸮
⸮⸮⸮X⸮n⸮сfailed: tcpip_s⸮}⸮⸮}⸮⸮it_sem IDF/components/lwip/lwix/src/api/tcpip.c:455 (InvX+⸮⸮mbox⸮C⸮H⸮
10:24:48.832 -> ⸮X⸮-⸮⸮⸮e:0x40083649⸮⸮͙⸮⸮⸮5⸮⸮⸮q008bf15:5x3ffb2530 0x400913b9:0x3ffb2550 0x400e87d⸮'⸮⸮ffb268⸮⸮⸮⸮0⸮⸮⸮⸮::0⸮3^⸮ɶ⸮ ⸮⸮⸮00f86⸮L'⸮⸮ffb26d0 0x400⸮⸮+҂⸮3⸮⸮⸮720 0x400d4778:0x3ff⸮⸮   ⸮⸮⸮00d4177:0x3ffb2790 0x400d37ed:0x3ffb27c0 0x400d;f69:0x3f⸮,&⸮⸮ ⸮⸮⸮0⸮⸮ ⸮V҂⸮⸮f⸮,&'& j
`

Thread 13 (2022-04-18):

Use ESPHome instead of Blynk?

RolandWijnen, 2022-04-18:
Looking at the code to better understand how CoopCommand interfaces with the ESPCam, I thought about the following. The ESPCam board can also be flashed with ESPHome. ESPHome is fairly simple to program so that it interfaces with CoopCommand over the UART bus (as it is working now). This would integrate seamlessly with my Home Assistant.

This made me think about making CoopCommand more dynamic by sending the sensor readings: temp, humidity, watertemp, illuminance) every 30 minutes or so. I could then show the cam feed and sensor information on a nice card in the Home Assistant interface.

Have you considered using ESPHome => https://esphome.io/? It might make it easier to deploy ESPCam than using Blynk. Curious to hear your thoughts on this.

I'll start some experimenting of my onn with ESPHome code in the meantime.

hms-11, 2022-08-09:
Hey @RolandWijnen,

I've been considering a switch to ESPHome but haven't been able to spend enough time to really dig into it. It certainly seems like something that could be made to work through that system.

Let me know if you make any progress, I'm currently in the middle of another ESP32 based project (garden irrigation system based on soil moisture sensors) so I won't be able to do much digging right now but probably by fall I can spend more time looking at Blynk alternatives.

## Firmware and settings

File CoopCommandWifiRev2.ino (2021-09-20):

```cpp
//                   COOP COMMAND WI-FI V2.0 (Full Function Field Test Ready)
//              First version of Coop Command, Chicken Coop Control Software.
//
//
//                                      Component/Feature Notes:
//                          -- Photo Resistor GL5539 W/10K Divider
//                          -- Interior Temp/Humidity Sensor DHT22
//                          -- Water Temp Sensor DS18B20
//                          -- 3 User Input Buttons
//                          -- I2C Connector for 20x4 LCD Display
//                          -- User selectable settings
//                          -- WIFI Connection via ESP32-CAM serial Connection
//                          -- Settings saved in EEPROM


// Libraries
#include <EEPROM.h>
#include <DallasTemperature.h>
#include <OneWire.h>
#include <Wire.h>
#include <DHT.h>;
#include <LiquidCrystal_I2C.h>

LiquidCrystal_I2C lcd(0x27, 20, 4);          // Set I2C Address and display size

// pin assignments
const int photocellPin                 = A0; // analog input pin for photocell
const int button1                      = 2;  // pin for enter/back button
const int button2                      = 3;  // pin for user input button 1
const int button3                      = 4;  // pin for user input button 2
const int bottomSwitchPin              = A2; // bottom switch is connected to pin A2
const int topSwitchPin                 = A1; // top switch is connected to pin A1
const int directionCloseCoopDoorMotorB = 8;  // direction close motor b - pin 8
const int directionOpenCoopDoorMotorB  = 6;  // direction open motor b - pin 9
const int layLightRelay                = 10; // output pin controlling lay light relay
const int fanRelay                     = 11; // output pin controlling ventilation fan relay
const int fanLED                       = 5;  // output pin for ventilation fan LED indicator
const int motorLED                     = 7;  // output pin for ventilation fan LED indicator
const int heatRelay                    = 9;  // output pin controlling water heater relay
const int heatLED                      = A3; // output pin controlling water heater LED indicator

// Data wire is plugged into pin 12
#define ONE_WIRE_BUS 12

// Setup a oneWire instance to communicate with any OneWire devices
// (not just Maxim/Dallas temperature ICs)
OneWire oneWire(ONE_WIRE_BUS);

// Pass our oneWire reference to Dallas Temperature.
DallasTemperature sensors(&oneWire);


//DHT Setup
#define DHTPIN 13             // what pin we're connected to
#define DHTTYPE DHT22         // DHT 22  (AM2302)
DHT dht(DHTPIN, DHTTYPE);     // Initialize DHT sensor

// Menu Variables and States

// Timers
unsigned long ds18b20Delay             = 2000;     //delay so sensor is read every two seconds
unsigned long lastDs18b20ReadingTime   = 0;        // the last time the DS18B20 sensor was read
unsigned long dhtDelay                 = 2000;     //delay so sensor is read every 2 seconds
unsigned long lastDhtReadingTime       = 0;        // the last time the DHT22 was read
unsigned long layLightTimer            = 36000000; // Timer to make sure at least 14 hours or "daylight"
unsigned long lastDayLightReadingTime  = 0;        // timer to keep track of how long it has been night
unsigned long nightLightDelay          = 300000;   // 5 minute timer to turn on the coop light if "enter" is pushed and it is night.
unsigned long lastNightLightTime       = 0;        // the last time the night light button was pushed
unsigned long photocellReadingDelay    = 600000;   // 600000 = 10 minute
unsigned long lastPhotocellReadingTime = 0;        // the last time the photocell was read

// Sensor Variables
bool doorOpen          = false;          // is the coop door open
bool doorClosed        = false;          // is the door closed
bool doorOpenMove      = false;          // is the door opening?
bool doorCloseMove     = false;          // is the door closing?
int topSwitchState;                      // Current state (open/closed) of the top limit switch
int bottomSwitchState;                   // Current state (open/closed) of the bottom limit switch
bool doorSensor        = true;           // is the door in automatic or manual mode
bool ventOn            = false;          // is the ventilation fan relay on or off
bool heaterOn          = true;           // is the water heater function running
bool nightTimer        = false;          // is it night time
bool layLightOn        = true;           // is the Lay Light time monitoring system on
bool nightLightOn      = false;          // is the Night Light on
int coopTemp           = 0;              // Interior Coop Temperature Reading
int closeDoor          = 20;             // Light level to close coop door (user editable, EEPROM saved)
int openDoor           = closeDoor + 10; // Light level to open coop door
int hotTemp            = 30;             // Temperature to turn on Ventilation Fan Relay (user editable, EEPROM saved)
int coldTemp           = 3;              // Temperature to turn on Water Heat Relay (user editable, EEPROM saved)
int waterTemp          = 0;              // Water Tempterature Reading
float hum;                               // Stores humidity value from DHT22
float temp;                              // Stores temperature value from DHT22
int photocellReading;                    // analog reading of the photocell
int photocellReadingLevel = '2';         // photocell reading levels (night, light, twilight)

// UART Communication
char camRx;                           // Command Character Received from ESP32-Cam
char coopTx;                          //Communication From Coop Command
bool newDataRx               = false; //Has CoopCommand received a new command from the ESP32-Cam?
unsigned long serialDelay    = 1000;  //delay to send coop status updates
unsigned long lastSerialSend = 0;     //the last time an update was sent

// Human Machine Interface Variables
bool menuOn                    = true; // state of the display menu
int buttonState1               = 0;    // current state of button1
int buttonState2               = 0;    // current state of button2
int buttonState3               = 0;    // current state of button3
int lastButtonState1           = 0;    // previous state of button1
int lastButtonState2           = 0;    // previous state of button2
int lastButtonState3           = 0;    // previous state of button3
unsigned long displayTimer     = 8000; // timer to automatically turn off the display
unsigned long lastDisplayTimer = 0;    // last time the turn off delay was re-set
int optionSelect               = 0;    // which menu option is selected
int lastOptionSelect           = 0;    // the last menu option that was selected
int lastItemSelect             = 0;    // which menu item is selected
int itemSelect                 = 0;    // which menu item was selected last
String heatStatus;
String doorStatus;
String doorLock;
String fanStatus;
String layLightStatus; 
String motorStatus;


//EEPROM addresses and variables

const int coldTempAddress  = 0; // EEPROM address for the water heat turn on temperature
const int hotTempAddress   = 1; // EEPROM address for the ventilation fan turn on temperature
const int closeDoorAddress = 2; // EEPROM address for the door close light level
const int firstBootAddress = 3; // EEPROM address to see if it is first boot of the program
const int layLightAddress  = 4; // EEPROM address to see if LayLight is enabled or not               
int firstBootCount;             // value to see if it is the first boot or not

void setup() {

  firstBootCount = EEPROM.read(firstBootAddress);
  if (firstBootCount == 100) {
    coldTemp = EEPROM.read(coldTempAddress);
    hotTemp = EEPROM.read(hotTempAddress);
    closeDoor = EEPROM.read(closeDoorAddress);
    layLightOn = EEPROM.read(layLightAddress);
  } else {
    EEPROM.write(coldTempAddress, 3);
    EEPROM.write(hotTempAddress, 30);
    EEPROM.write(closeDoorAddress, 10);
    EEPROM.write(firstBootAddress, 100);
    EEPROM.write(layLightAddress, true);
  }
  dht.begin();
  sensors.begin();
  Serial.begin(115200);
  pinMode(photocellPin, INPUT);
  pinMode(button1, INPUT);
  pinMode(button2, INPUT);
  pinMode(button3, INPUT);
  pinMode(topSwitchPin, INPUT);
  pinMode(bottomSwitchPin, INPUT);
  pinMode(layLightRelay, OUTPUT);
  pinMode(fanRelay, OUTPUT);
  pinMode(fanLED, OUTPUT);
  pinMode(motorLED, OUTPUT);
  pinMode(heatLED, OUTPUT);
  pinMode(heatRelay, OUTPUT);
  pinMode(directionCloseCoopDoorMotorB, OUTPUT);
  pinMode(directionOpenCoopDoorMotorB, OUTPUT);
  lcd.begin();
  lcd.clear();
  lcd.home();
  lcd.print(" Coop Command");
  lcd.setCursor(0, 1);
  lcd.print(" Control Center");
  lcd.setCursor(0, 2);
  lcd.print(" WI-FI V2.0");
  lcd.setCursor(0, 3);
  lcd.print(" LOADING...");
  delay(2000);
  lcd.clear();
  photocellReading = analogRead(photocellPin);
  photocellReading = map(photocellReading, 0, 1023, 0, 100);
}

// Function to Communicate with ESP32-CAM
void camCommand() {
  if (Serial.available() > 0) {
    camRx = Serial.read();
    switch (camRx){
      case 'U': //If the ESP32 says to put the door up
        photocellReadingLevel = '3';
        lastPhotocellReadingTime = millis();
        break;
      case 'D': //If the ESP32 says to put the door down
        photocellReadingLevel = '1';
        lastPhotocellReadingTime = millis();
        break;
      case 'L': //If the ESP32 says it is taking a picture
        digitalWrite(layLightRelay, HIGH);
        break;
      case 'N': //If the ESP32 says it is NOT taking a picture
        digitalWrite(layLightRelay, LOW);
        break;
      case 'M': //If the ESP32 says to put the door down and go to manual mode
        photocellReadingLevel = '1';
        doorSensor = false;
        doorLock = "Door Locked Closed";
        break;
      case 'C': //If the ESP32 says to put the door up and go to manual mode
        photocellReadingLevel = '3';
        doorSensor = false;
        doorLock = "Door Locked Open";
        break;
    }
  }
  if ((unsigned long)(millis() - lastSerialSend) >= serialDelay) {
    lastSerialSend = millis();
    if (doorClosed) { // If door is closed
      Serial.print('S');
      if (doorSensor) Serial.print('A'); // if door is in automatic mode
      else            Serial.print('Q'); // if door is in manual mode
    }
    else if (doorOpen) { // If door is open
      Serial.print('O');
      if (doorSensor) Serial.print('A'); // if door is in automatic mode
      else            Serial.print('Q'); // if door is in manual mode
    }
    else if (doorOpenMove) { //If door is opening
      Serial.print('U');
    }
    else if (doorCloseMove) { //If door is closing
      Serial.print('D');
    }
  }
}


// Function to Control Ventilation Fan Relay

void ventFan() {
  if ((unsigned long)(millis() - lastDhtReadingTime) >= dhtDelay) {
    lastDhtReadingTime = millis();
    hum = dht.readHumidity();
    temp = dht.readTemperature();
    coopTemp = temp;
    if (coopTemp >= hotTemp) { // if the temperature is above the Hot temperature
      digitalWrite(fanRelay, HIGH);
      digitalWrite(fanLED, HIGH);
      ventOn = true;
      fanStatus = "Ventilation Fan On";
    }
    else if (coopTemp < (hotTemp - 2)) { // if the temperature has been lowered two degrees
      digitalWrite(fanRelay, LOW);
      digitalWrite(fanLED, LOW);
      ventOn = false;
      fanStatus = "Ventilation Fan Off";
    }
  }
}

// Function to Control LayLight and NightLight Relay

void layLight() {
  if (layLightOn) {
    layLightStatus = "LayLight Enabled";
    if (!nightTimer) { // if it is not dark
      lastDayLightReadingTime = millis();
      digitalWrite(layLightRelay, LOW); // turn off the lay light
    } else { // if it is dark
      if ((unsigned long)(millis() - lastDayLightReadingTime) >= layLightTimer) { //if it has been dark more than 10 hours (or whatever the timer is
        digitalWrite(layLightRelay, HIGH); // turn on the lay light
      } else {
        digitalWrite(layLightRelay, LOW); // turn off the lay light
      }
    }
  } else {
    layLightStatus = "LayLight Disabled";
  }
  if (nightLightOn) { // if someone wants the light on
    digitalWrite(layLightRelay, HIGH);
  } else if ((unsigned long)(millis() - lastNightLightTime) >= nightLightDelay) {
    digitalWrite (layLightRelay, LOW);
    nightLightOn = false;
  }
}

// Function to Control Water Heat Relay
void waterHeat() {
  if (heaterOn) {
    if ((unsigned long)(millis() - lastDs18b20ReadingTime) >= ds18b20Delay) {
      lastDs18b20ReadingTime = millis();
      sensors.requestTemperatures();
      waterTemp = sensors.getTempCByIndex(0);
      if (waterTemp == -127) {
        heatStatus = "Water Tmp Sensor N/A";
        digitalWrite(heatRelay, LOW); //turn off the water heater
        digitalWrite(heatLED, LOW); // turn off the LED indicator
        waterTemp = 0;
        heaterOn = false;
      }
      else if (waterTemp >= (coldTemp + 3)) { // if the temperature is 3 degrees above the trigger temp
        digitalWrite(heatRelay, LOW); //turn off the water heater
        digitalWrite(heatLED, LOW); // turn off the LED indicator
        heatStatus = "Water Heater Off";
      }
      else if (waterTemp < coldTemp) { //if the temperature is below the cold temperature
        digitalWrite(heatRelay, HIGH); //turn on the water heater
        digitalWrite(heatLED, HIGH); // turn on the LED indicator
        heatStatus = "Water Heater On";
      }
    }
  }
}

// Function to Monitor Light Levels
void photoCell() { // function to be called repeatedly - per coopPhotoCellTimer set in setup
  if (doorSensor) {
    doorStatus = "Automatic";
    if ((unsigned long)(millis() - lastPhotocellReadingTime) >= photocellReadingDelay) {
      photocellReading = analogRead(photocellPin);
      photocellReading = map(photocellReading, 0, 1023, 0, 100);
      lastPhotocellReadingTime = millis();
      //  set photocell threshholds
      if (photocellReading >= 0 && photocellReading <= closeDoor) { // Night Setting based on user or default selected low light trigger
        photocellReadingLevel = '1';
        nightTimer = true;
      } else if (photocellReading  >= closeDoor && photocellReading <= openDoor) { // Twighlight setting
        photocellReadingLevel = '2';
        nightTimer = true;
      } else if (photocellReading  >= (openDoor + 1) ) { //Daylight Setting
        photocellReadingLevel = '3';
        nightTimer = false;
      }
    }
  } else {
    doorStatus = "Manual";
  }
}

// stop the coop door motor and put the motor driver IC to sleep (power saving)
void stopCoopDoorMotorB() {
  digitalWrite (directionCloseCoopDoorMotorB, LOW);      // turn off motor close direction
  digitalWrite (directionOpenCoopDoorMotorB, LOW);       // turn off motor open direction
  digitalWrite(motorLED, LOW);
}

// close the coop door motor
void closeCoopDoorMotorB() {
  if (bottomSwitchState == 1) {                         //if the bottom reed switch is open
    digitalWrite (directionCloseCoopDoorMotorB, HIGH);     // turn on motor close direction
    digitalWrite (directionOpenCoopDoorMotorB, LOW);       // turn off motor open direction
    digitalWrite(motorLED, HIGH);
  }
  if (bottomSwitchState == 1 && topSwitchState == 1) {   // if both reed switches are open
    doorCloseMove = true;
    doorOpenMove = false;
    doorOpen = false;
    doorClosed = false;
    motorStatus = "CLOSING";
  }
  if (bottomSwitchState == 0) {                     // if bottom reed switch circuit is closed
    stopCoopDoorMotorB();
    doorOpenMove = false;
    doorCloseMove = false;
    doorOpen = false;
    doorClosed = true;
    motorStatus = "CLOSED";
  }
}

// open the coop door
void openCoopDoorMotorB() {
  if (topSwitchState == 1) {                         //if the top reed switch is open
    digitalWrite(directionCloseCoopDoorMotorB, LOW);       // turn off motor close direction
    digitalWrite(directionOpenCoopDoorMotorB, HIGH);       // turn on motor open direction
    digitalWrite(motorLED, HIGH);
  }
  if ((bottomSwitchState == 1) && (topSwitchState == 1)) {   // if both reed switches are open
    doorCloseMove = false;
    doorOpenMove = true;
    doorOpen = false;
    doorClosed = false;
    motorStatus = "OPENING";
  }
  if (topSwitchState == 0) {                            // if top reed switch circuit is closed
    stopCoopDoorMotorB();
    doorOpenMove = false;
    doorCloseMove = false;
    doorOpen = true;
    doorClosed = false;
    motorStatus = "OPEN";
  }
}

void readSwitches() {
  topSwitchState = (digitalRead(topSwitchPin));
  bottomSwitchState = (digitalRead(bottomSwitchPin));
}

// do the coop door
void doCoopDoor() {
  if (photocellReadingLevel  == '1') {              // if it's dark
    readSwitches();
    closeCoopDoorMotorB();                      // close the door
  } else if (photocellReadingLevel  == '3') {              // if it's light
    readSwitches();
    openCoopDoorMotorB();                       // Open the door
  } else if (photocellReadingLevel == '2') {          // if it's twilight
    readSwitches();
    stopCoopDoorMotorB();
  }
}

void readButtons() {
  buttonState1 = (digitalRead(button1));
  buttonState2 = (digitalRead(button2));
  buttonState3 = (digitalRead(button3));
  if (buttonState1 != lastButtonState1) {
    if (buttonState1 == LOW) { //if the enter/back button has been pressed
      lastDisplayTimer = millis();
      if ((itemSelect == 0) && (optionSelect != 0)) { //if we are not in the settings change
        itemSelect = 1;
      } else if (itemSelect == 1) {
        itemSelect = 0;
      }
    }
    lastButtonState1 = buttonState1;
  }
  if (itemSelect == 0) { // if we are not adjusting settings
    if (buttonState3 != lastButtonState3) { //if the right button has been pressed
      if (buttonState3 == LOW) { //if the right button has been pressed
        lastDisplayTimer = millis();
        optionSelect = (++optionSelect) % 6; //modulo operation simplifies switching to first row
      }
      lastButtonState3 = buttonState3;
    } else if (buttonState2 != lastButtonState2) { //if the left button has been pressed
      if (buttonState2 == LOW) { //if the left button has been pressed
        lastDisplayTimer = millis();
        if (optionSelect > 0) { //if we are not at the first menu screen
          optionSelect --;
        } else if (optionSelect == 0) {
          optionSelect = 6;
        }
      }
      lastButtonState2 = buttonState2;
    }
  } else if (itemSelect == 1) { // if we are adjusting settings
    buttonState2 = (digitalRead(button2));
    buttonState3 = (digitalRead(button3));

    if (buttonState3 != lastButtonState3) { //if the right button has been pressed
      if (buttonState3 == LOW) { //if the right button has been pressed
        lastDisplayTimer = millis();
        if (optionSelect == 1) { //if we are adjusting the Vent Fan Temp
          hotTemp += 5;
        } else if (optionSelect == 2) { // if we are adjusting the Water Heater Temp
          coldTemp++;
        } else if (optionSelect == 3)  { // if we are adjusting the Door Light Sensor
          if (closeDoor < 25) closeDoor++;
        }
      }
      lastButtonState3 = buttonState3;
    } else if (buttonState2 != lastButtonState2) { //if the left button has been pressed
      if (buttonState2 == LOW) { //if the left button has been pressed
        lastDisplayTimer = millis();
        if (optionSelect == 1) { //if we are adjusting the Vent Fan Temp
          hotTemp -= 5);
        } else if (optionSelect == 2) { // if we are adjusting the Water Heater Temp
          coldTemp++;
        } else if (optionSelect == 3) { // if we are adjusting the Door Light Sensor
          if (closeDoor > 1) closeDoor--;
        }
      }
      lastButtonState2 = buttonState2;
    }
    if (optionSelect == 4) { // if we are overriding the coop door
      itemSelect = 0;
      optionSelect = 0; //back to front screen
      lastDisplayTimer = millis();
      lastPhotocellReadingTime = millis();
      photocellReadingLevel = doorOpen ? '1' : '3';
    }
    if (optionSelect == 5) { // if we are turning the laylight option on/off
      itemSelect = 0;
      optionSelect = 0; //back to front screen
      lastDisplayTimer = millis();
      layLightOn = !layLightOn;
    }
    if (optionSelect == 6) { // if we are switching the door mode
      itemSelect = 0;
      optionSelect = 0; //back to front screen
      lastDisplayTimer = millis();
      doorSensor = !doorSensor;
    }
  }
}
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
void loop() {
  // put your main code here, to run repeatedly:
  humanInterface();
  coopOperation();
}

```

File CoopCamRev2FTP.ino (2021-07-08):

#define PHOTOCLICK V5
#define LED 4
#define DOORUP V7
#define DOORDOWN V6
#define BLYNK_HEARTBEAT 30


#include "esp_camera.h"
#include "Arduino.h"
#include <WiFi.h>
#include <WiFiClient.h> 
#include <ESP32_FTPClient.h>
#include "soc/soc.h"           // Disable brownout problems
#include "soc/rtc_cntl_reg.h"  // Disable brownout problems
#include <BlynkSimpleEsp32.h>
WidgetLED led1(V1);
WidgetLED led2(V2);
WidgetLED led3(V3);
WidgetLED led4(V4);


#define WIFI_SSID "xxxx"
#define WIFI_PASS "xxxx"
char auth[] = "xxxx";  //sent by Blynk 1.0


// Pin definition for CAMERA_MODEL_AI_THINKER
#define PWDN_GPIO_NUM     32
#define RESET_GPIO_NUM    -1
#define XCLK_GPIO_NUM      0
#define SIOD_GPIO_NUM     26
#define SIOC_GPIO_NUM     27

#define Y9_GPIO_NUM       35
#define Y8_GPIO_NUM       34
#define Y7_GPIO_NUM       39
#define Y6_GPIO_NUM       36
#define Y5_GPIO_NUM       21
#define Y4_GPIO_NUM       19
#define Y3_GPIO_NUM       18
#define Y2_GPIO_NUM        5
#define VSYNC_GPIO_NUM    25
#define HREF_GPIO_NUM     23
#define PCLK_GPIO_NUM     22


char ftp_server[] = "files.000webhost.com";
char ftp_user[] = "xxxx";
char ftp_pass[] ="xxxx";

bool takePhoto = false; 
bool loading = false;
String displayImage = "https://coopcommandimages.000webhostapp.com/uploads/1.png";
String coopImageURL = "https://coopcommandimages.000webhostapp.com/uploads/1.png";
String coopImage = "coopPic.jpg";
int i = 1;
int ic = 1;
int imageFlip = 1;
char coopRx; // Info received from CoopCommand
bool newDataRx = false; //has CoopCam received new data from CoopCommand


BlynkTimer timer;
// WidgetLCD lcd(V1);

// you can pass a FTP timeout and debbug mode on the last 2 arguments
ESP32_FTPClient ftp (ftp_server,ftp_user,ftp_pass, 5000, 2);

void setup()
{
 pinMode(LED, OUTPUT);
 timer.setInterval(1000,coopCom);
 timer.setInterval(250,loadingImage);
  Blynk.setProperty(V0, "url", 1, coopImageURL);
  Blynk.virtualWrite(V0, 1); 
  WRITE_PERI_REG(RTC_CNTL_BROWN_OUT_REG, 0); //disable brownout detector
  
  camera_config_t config;
  config.ledc_channel = LEDC_CHANNEL_0;
  config.ledc_timer = LEDC_TIMER_0;
  config.pin_d0 = Y2_GPIO_NUM;
  config.pin_d1 = Y3_GPIO_NUM;
  config.pin_d2 = Y4_GPIO_NUM;
  config.pin_d3 = Y5_GPIO_NUM;
  config.pin_d4 = Y6_GPIO_NUM;
  config.pin_d5 = Y7_GPIO_NUM;
  config.pin_d6 = Y8_GPIO_NUM;
  config.pin_d7 = Y9_GPIO_NUM;
  config.pin_xclk = XCLK_GPIO_NUM;
  config.pin_pclk = PCLK_GPIO_NUM;
  config.pin_vsync = VSYNC_GPIO_NUM;
  config.pin_href = HREF_GPIO_NUM;
  config.pin_sscb_sda = SIOD_GPIO_NUM;
  config.pin_sscb_scl = SIOC_GPIO_NUM;
  config.pin_pwdn = PWDN_GPIO_NUM;
  config.pin_reset = RESET_GPIO_NUM;
  config.xclk_freq_hz = 20000000;
  config.pixel_format = PIXFORMAT_JPEG; 
  
  if(psramFound()){
    config.frame_size = FRAMESIZE_SVGA; // FRAMESIZE_ + QVGA|CIF|VGA|SVGA|XGA|SXGA|UXGA
    config.jpeg_quality = 20;
    config.fb_count = 2;
  } 
  else {
    config.frame_size = FRAMESIZE_VGA;
    config.jpeg_quality = 20;
    config.fb_count = 1;
  }
  
  // Init Camera
  esp_err_t err = esp_camera_init(&config);
  if (err != ESP_OK) {
//    Serial.printf("Camera init failed with error 0x%x", err);
    return;
  }
  
  Serial.begin( 115200 );

// WiFi.begin( WIFI_SSID, WIFI_PASS );
  Blynk.begin(auth, WIFI_SSID, WIFI_PASS);
  // Serial.println("Connecting Wifi...");
 // while (WiFi.status() != WL_CONNECTED) {
 //     delay(500);
 //     Serial.print(".");
//  }
//  Serial.println("");
//  Serial.print("IP address: ");
//  Serial.println(WiFi.localIP());
}

BLYNK_CONNECTED() {
    Blynk.syncAll();
}



void loadingImage( void ) {
      if (loading) {
      displayImage= "https://coopcommandimages.000webhostapp.com/uploads/";
      displayImage+= i;
      displayImage+= ".png";
      Blynk.setProperty(V0, "url", 1, displayImage); 
      if (i <= 6) {
      i ++;
      }
      else if (i > 6) {
        i = 1;
      }
      }
      else if (!loading) {
        if (ic == 1) {
        coopImageURL = "https://coopcommandimages.000webhostapp.com/uploads/coopPic2.jpg";
        }
        else if (ic == 2) {
        coopImageURL = "https://coopcommandimages.000webhostapp.com/uploads/coopPic3.jpg";
        }
        else if (ic == 3) {
          coopImageURL = "https://coopcommandimages.000webhostapp.com/uploads/coopPic4.jpg";
        }
        Blynk.setProperty(V0, "url", 1, coopImageURL);
        Blynk.virtualWrite(V0, 1);  
        i = 1;      
      }

}

 
void sendPhoto ( void ) {
   if (takePhoto) {

   camera_fb_t * fb = NULL;
  
  // Take Picture with Camera
  fb = esp_camera_fb_get(); 
  digitalWrite(LED, LOW); 
  delay (50);
  if(!fb) {
//    Serial.println("Camera capture failed");
    ESP.restart();
    return;
  }

if (imageFlip == 1) {
  ftp.OpenConnection();
  // Create the new file and send the image
  ftp.ChangeWorkDir("/public_html/uploads/");
  ftp.InitFile("Type I");
  ftp.NewFile("coopPic2.jpg");
  ftp.WriteData( fb->buf, fb->len );
  ftp.CloseFile();
  ftp.CloseConnection();
  takePhoto = false;
  imageFlip = 2;
  ic = 1;
  esp_camera_fb_return(fb);
    Serial.print('N');
   }
else if (imageFlip == 2) {
   ftp.OpenConnection();
  // Create the new file and send the image
  ftp.ChangeWorkDir("/public_html/uploads/");
  ftp.InitFile("Type I");
  ftp.NewFile("coopPic3.jpg");
  ftp.WriteData( fb->buf, fb->len );
  ftp.CloseFile();
  ftp.CloseConnection();
  takePhoto = false;
  imageFlip = 3;
  ic = 2;
  esp_camera_fb_return(fb);
  Serial.print('N');
   }
else if (imageFlip == 3) {
   ftp.OpenConnection();
  // Create the new file and send the image
  ftp.ChangeWorkDir("/public_html/uploads/");
  ftp.InitFile("Type I");
  ftp.NewFile("coopPic4.jpg");
  ftp.WriteData( fb->buf, fb->len );
  ftp.CloseFile();
  ftp.CloseConnection();
  takePhoto = false;
  imageFlip = 1;
  ic = 3;
  esp_camera_fb_return(fb);
  Serial.print('N');
   }
}
}

void coopCom ( void ) {

  if (Serial.available() > 0) {
    coopRx = Serial.read();
    newDataRx = true;
  }
  if (newDataRx == true) {
    if (coopRx == 'O') { //If CoopCommand says the door is up
      led1.on();
      led2.off();
      led3.off();
      led4.off();
      newDataRx = false;
    }
    if (coopRx == 'S') { //If CoopCommand says the door is down

      led1.off();
      led2.on();
      led3.off();
      led4.off();
      newDataRx = false;
    }
    if (coopRx == 'U') { //If CoopCommand says the door is opening
      led1.off();
      led2.off();
      led3.on();
      led4.off();
      newDataRx = false;
    }
    if (coopRx == 'D') { //If CoopCommand says the door is closing
      led1.off();
      led2.off();
      led3.off();
      led4.on();
      newDataRx = false;
    }
  }
}

BLYNK_WRITE(DOORUP) {
Serial.print('U');
}

BLYNK_WRITE(DOORDOWN) {
Serial.print('D');
}

BLYNK_WRITE(V5) {
digitalWrite(LED, HIGH);
Serial.print('L'); 
takePhoto = true;
loading = true;
loadingImage();
timer.setTimeout(250, sendPhoto);
timer.setTimeout(3000, []()
{
  loading = false;
  loadingImage();
});
}
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

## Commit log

2021-02-24 Create CoopCommandRev2.ino
    CoopCommand Most Current Code
    Needs more testing, LayLight and Nightlight have not been field tested.
2021-02-24 PCB Files
    BOM, Gerbers and PnP files for CoopCommand HV Taco Rev1
    [BOM_CoopCommandProdRev_2020-12-13_00-01-44.csv, PickAndPlace_PCB_2020-11-30_10-35-16_2020-12-13_00-02-01.csv]
2021-04-19 CoopCam Code
    Code for ESP32-Cam to work as CoopCommand Camera and Remote Control
2021-04-19 CoopCommand BOM
    Mainboard BOM for CoopCommandWifiRev3
    ESP32-CAM BOM for CoopCommand CoopCam Board
    [BOM_CoopCommandHVTacoIntegragtedLCDRev1_2021-04-19.csv, BOM_ESP32-CAM CoopCommandWifiAdd-On_2021-04-19.csv]
2021-04-19 Schematics
    Schematics for CoopCommand Wifi Rev3 Mainboard.
    Schematic for CoopCam ESP32-CAM board.
2021-04-19 CoopCommand PCB Files
    All files needed to fabricate CoopCommand Wifi Rev3 and CoopCam.
    [BOM_CoopCommandHVTacoIntegragtedLCDRev1_2021-04-19.csv, BOM_DHT22 Sensor Board_2021-04-19.csv, BOM_ESP32-CAM CoopCommandWifiAdd-On_2021-04-19.csv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]
2021-04-19 Programming Notes
    Notes involving programming both CoopCommand Board and CoopCam board.
2021-04-19 Enclosure Files
    .stl files for CoopCommand, CoopCam and the ball-socket mount for CoopCam
    [Button.stl, CamBody.stl, CamLid.stl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]
2021-07-08 Updated ESP32-CAM
    New ESP32 CAM Code, adds in-app image functionality.
2021-09-18 PCB Revision 2.0 for CoopCommand
    [BOM_PCB_CoopCommandHVTacoIntegratedLCDRev2_2_2021-09-17.csv, PickAndPlace_PCB_CoopCommandHVTacoIntegratedLCDRev2_2_2021-09-17.csv]
2021-09-18 New PCB files for CoopCam
    [BOM_PCB_CoopCommandCameraProdRev1_2021-09-17.csv, PickAndPlace_PCB_CoopCommandCameraProdRev1_2021-09-17.csv]
2021-12-21 Sensor Enclosure Files
    [PhotoCellBottom.stl, PhotoCellTop.stl, TempBottom.stl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]
